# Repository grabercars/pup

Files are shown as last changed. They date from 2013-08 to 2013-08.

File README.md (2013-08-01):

Cerberus Pup
========

Derivative of the Rostock 3D delta printer - 

[cc by sa 3.0]

Cerberus Pup
========

7/31/2013

Cerberus Pup is an experimental 3D Delta Robot printer that uses spectra filament for the vertical carriage drive system instead of traditional toothed belts. Please be aware that there will probably (and most likely) be significant changes and improvements made to this design. - A photo gallery of the Ceberus prototype can be found in the G+ gallery here: http://tinyurl.com/CerberusPup

A BOM is available here - http://tinyurl.com/Pup-BOM-Google-Spreadsheet - there are still some issues with the BOM, please contact Steve Graber to help correct any issues you find.

Print Files:

Qty - Filename

3 - 1x.125 aluminum bar.pdf

3 - 2x.125 aluminum bar.pdf

1 - Extruder_Lever.stl

1 - Extruder_Mount.stl

1 - Jslot_insert.stl

1 - JSlot_plate.stl

1 - Platform_and_Shroud_Assem_Traxxas.stl

1 - Pup_Base_Template.PDF

3 - Pup_Bottom_Bracket.stl

3 - Pup_Upper_Bracket.stl

3 - Pup_Upper_Idler_Adjuster_Bearing_Carrier.stl

3 - Upper_Idler_Axle_airtripper.stl

3 - Pup_Vertical_Carriage.stl

2 - VIKI_LCD_Panel_Side_Mounting_Bracket.stl

1 - Viki_Panel_Surround.stl

2 - Viki_to_Pup_Hangar_Bracket.stl (mirror 2nd copy)

Experimental Files: 

1 - Platform_Geomag_v2_with_shroud.stl

1 - Pup_vert_carriage_Geomag_v2.stl

You will need to print a set of Xnaron magnetic rods available here: http://www.thingiverse.com/thing:87839 - Your printer needs to be very accurate and you will have problems aligning the steel balls perfectly on the platform. This is why this feature is experimental as it was difficult to attach the balls to the ends of bolts with epoxy with any dimensional consistency.

Notes:

All machined parts required to build Cerberus Pup are now all available for purchase at http://3d.grabercars.com. They are manufactured on a CNC lathe to very tight tolerances.

SPECTRA FILAMENT VERTICAL CARRIAGE DRIVE SYSTEM:
Cerberus does not use belts or leadscrews. It uses a very strong braided filament called spectra. This is commonly used as fishing line. Cerberus uses 65lb test line. The drive system requires a threaded 'spool' or 'drive reel' that grabs the spectra very securely. CNC machined delrin filament drive reels are now available for purchase at 3d.grabercars.com - It is not recommended to use 3D printed drive reels because the print accuracy of your printer will suffer.

VERTICAL CARRIAGES:
The Cerberus vertical carriages move up and down the extrusion towers by rolling on 3 cnc machined delrin 'w' rollers per carriage. Each roller consists of a cnc machined delrin cover with two 623 bearing pressed in. The roller rides in the T-Slot of the OpenBeam or Misumi 1515 extrusion. This makes for a very smooth and accurate linear carriage system. Dual 623 V Rollers  can be purchased from 3d.grabercars.com

FILAMENT TENSION SYSTEM:
Due to the high tension required of the spectra filament drive, the upper idler adjuster bearing carrier requires one machined delrin V-Groove idler filament bearing per vertical tower, riding on an 8mm shaft. This upper idler bearing transfers the upward motion of the spectra filament at the top of the printer towers into downward motion. I used a printed 8mm idler bearing shaft borrowed from Airtrippers Bowden extruder (Search www.thingiverse.com) and manufactured the delrin V-Groove idlers with 8mm I.D. hole on a CNC lathe.

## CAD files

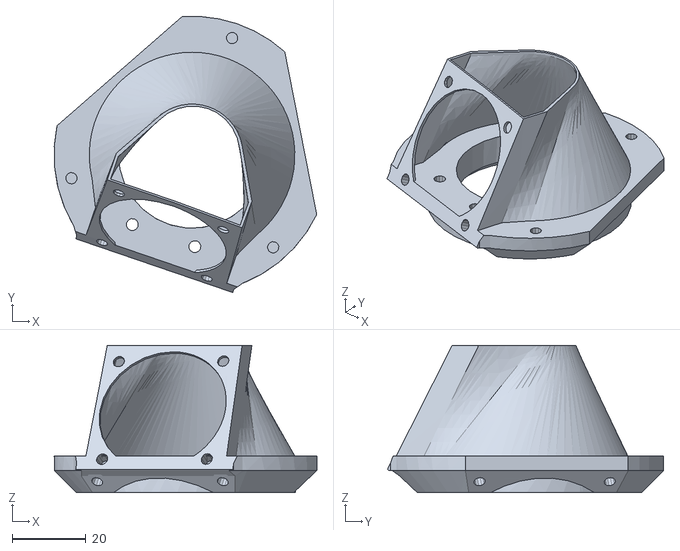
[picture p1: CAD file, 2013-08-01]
experimental/platform_Geomag_v2_with_shroud.STL
71.2 x 74.9 x 40.0

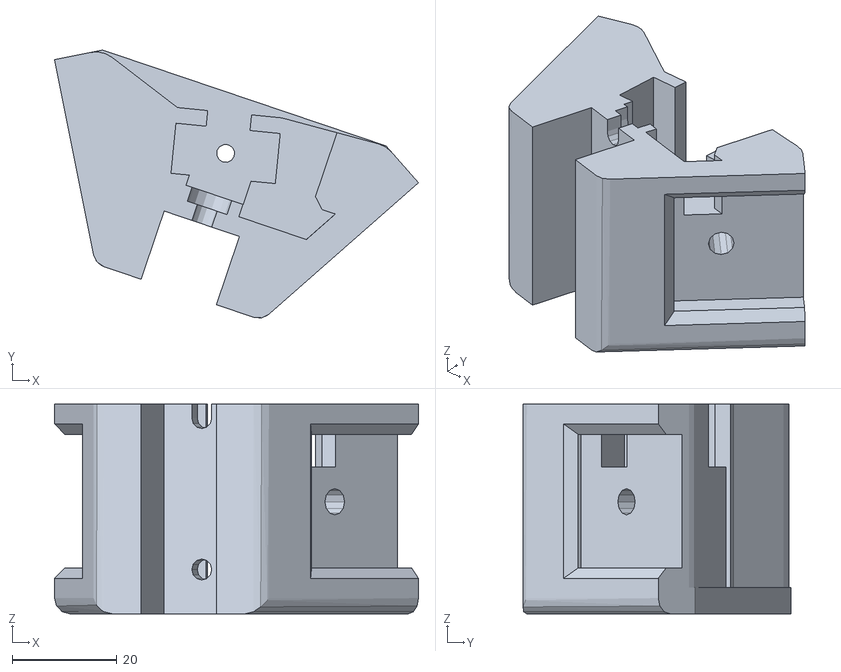
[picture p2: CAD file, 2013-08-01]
Pup_Upper_Bracket.stl
69.4 x 51.1 x 40.0

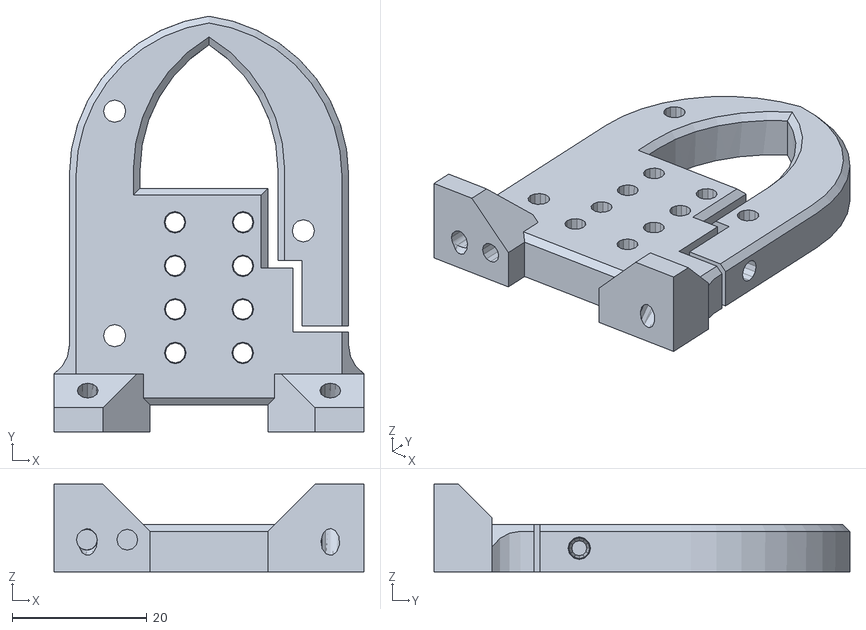
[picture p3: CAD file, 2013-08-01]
experimental/Pup_vert_carriage_Geomag_v2.STL
46.0 x 61.7 x 13.0

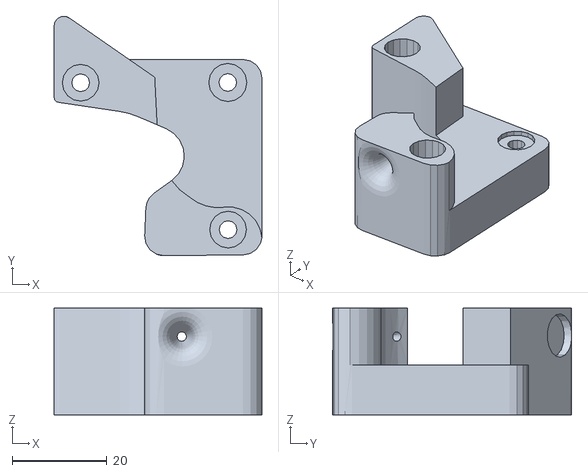
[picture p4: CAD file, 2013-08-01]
Extruder_Mount.stl
43.8 x 50.4 x 22.5

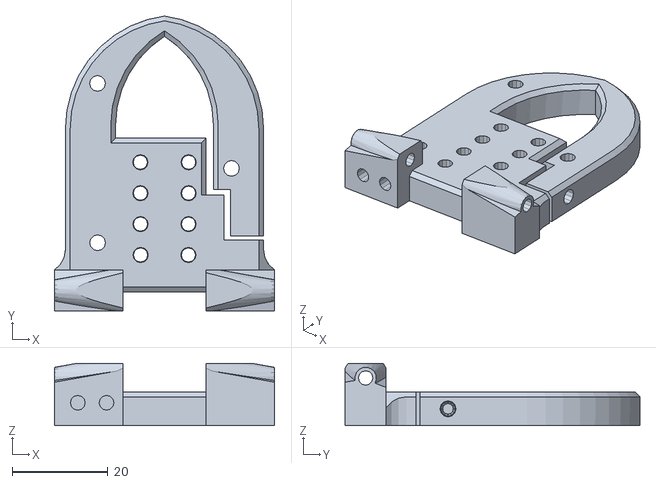
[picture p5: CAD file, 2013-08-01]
Pup_Vertical_Carriage.stl
46.0 x 61.7 x 13.0

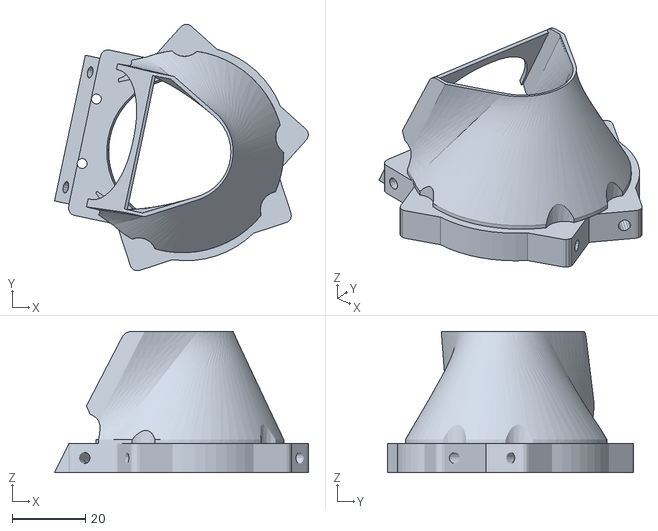
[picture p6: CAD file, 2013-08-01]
Platform_and_Shroud_Assem_Traxxas.stl
69.1 x 67.1 x 38.5

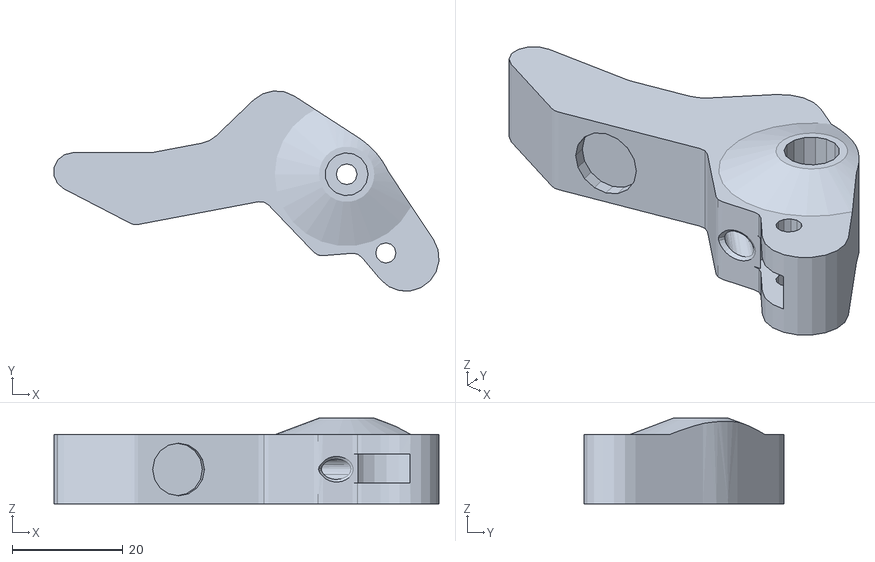
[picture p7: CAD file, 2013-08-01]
Extruder_Lever.stl
69.6 x 36.2 x 15.5

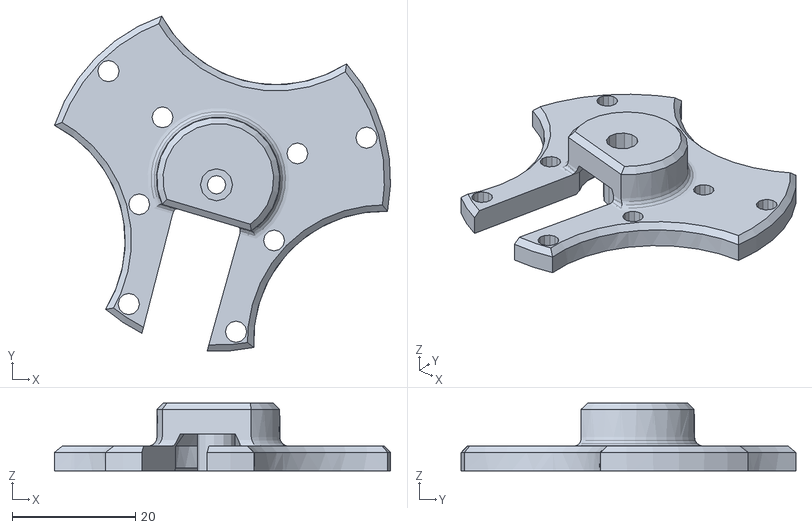
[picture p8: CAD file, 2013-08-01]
JSlot_plate.stl
54.6 x 54.4 x 11.0

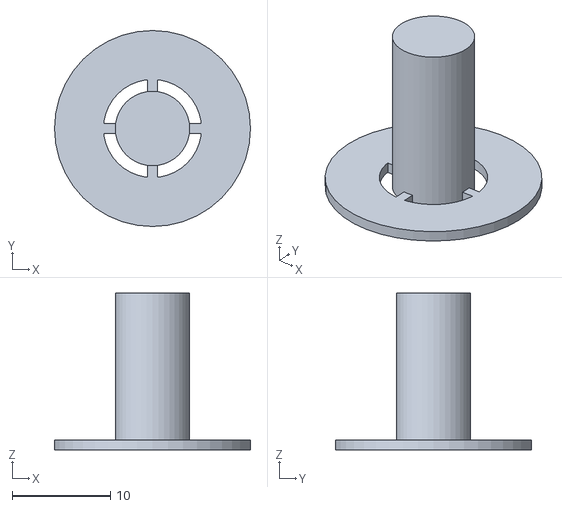
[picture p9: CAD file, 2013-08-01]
Upper_Idler_Axle_airtripper.stl
20.0 x 20.0 x 16.0

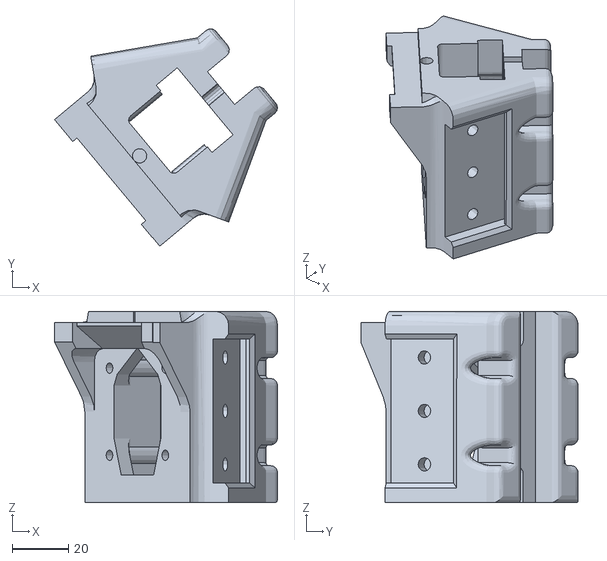
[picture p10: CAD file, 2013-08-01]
Pup_Bottom_Bracket.stl
79.3 x 77.2 x 68.0

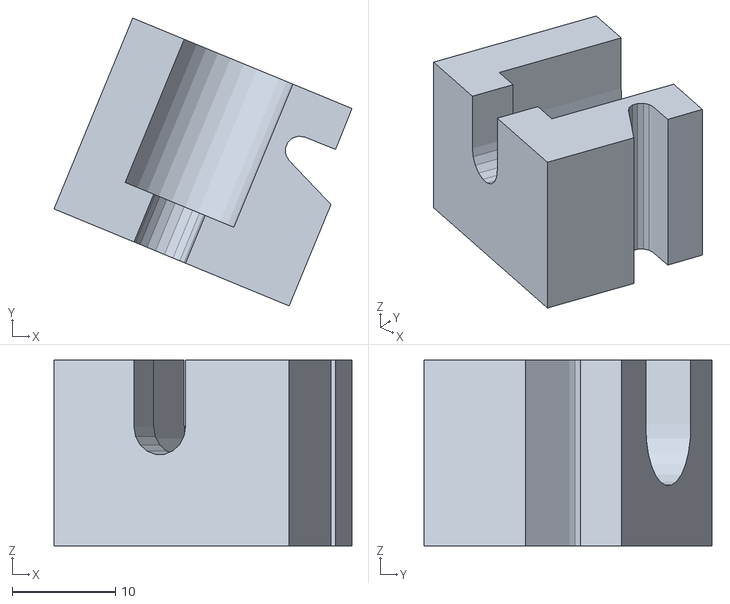
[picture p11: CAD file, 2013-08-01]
Viki_to_Pup_Hangar_Bracket.stl
28.9 x 27.9 x 18.0

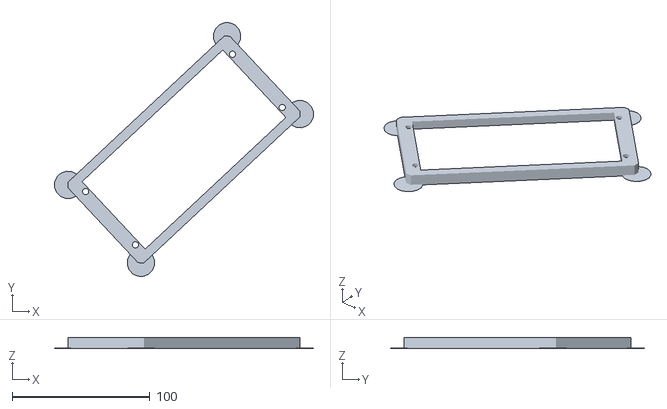
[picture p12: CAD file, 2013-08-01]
Viki_Panel_Surround.stl
187.8 x 184.0 x 8.00

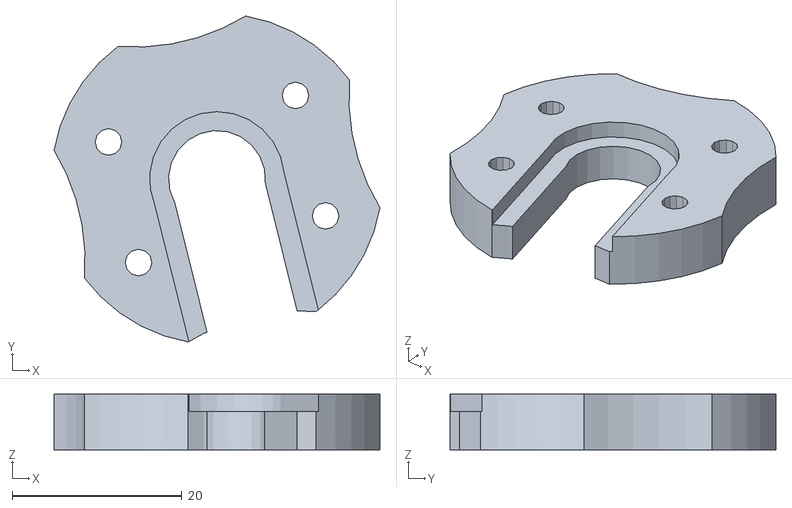
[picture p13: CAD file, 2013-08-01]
Jslot_insert.stl
38.4 x 38.4 x 6.56

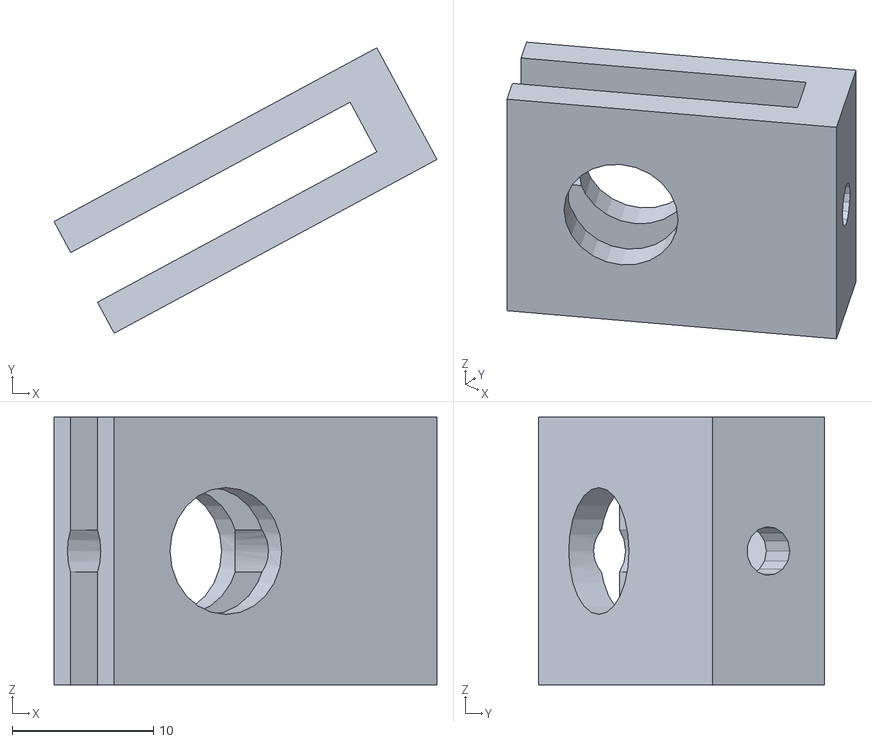
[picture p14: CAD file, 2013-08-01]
Pup_Upper_Idler_Adjuster_Bearing_Carrier.stl
27.2 x 20.3 x 19.0

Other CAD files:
VIKI_LCD_Panel_Side_Mounting_Bracket.stl

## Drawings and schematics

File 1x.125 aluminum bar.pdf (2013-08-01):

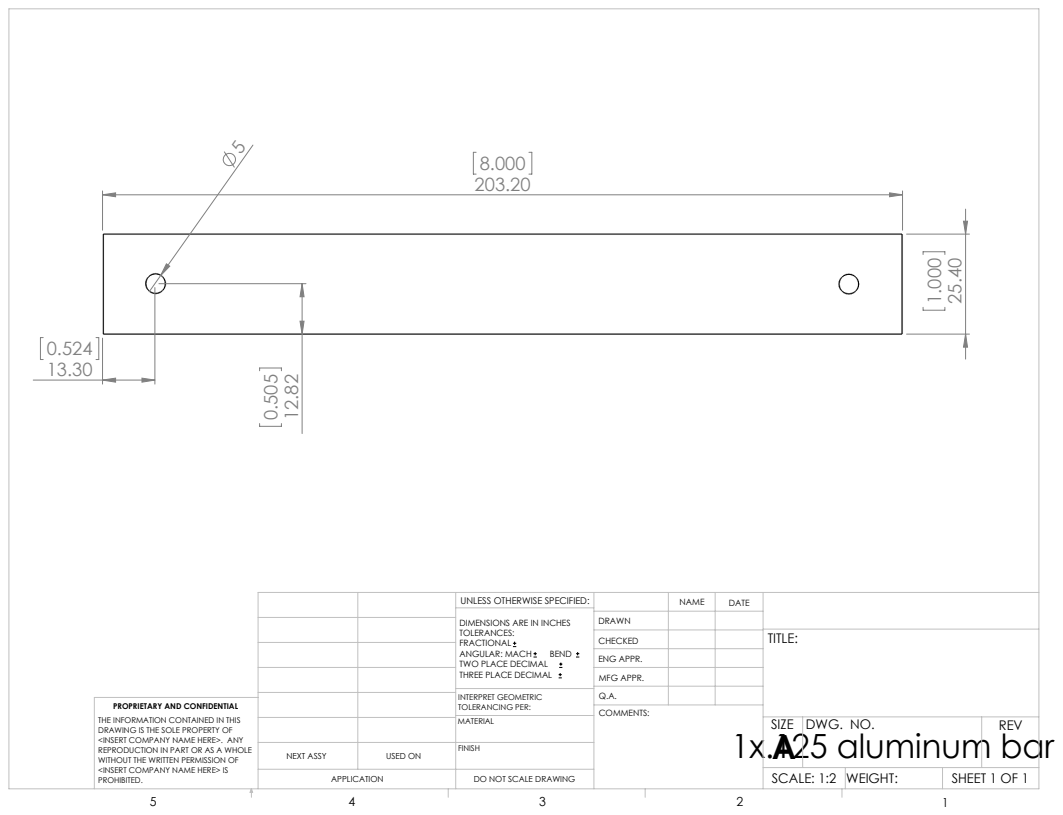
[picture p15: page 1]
1x.125 aluminum bar; SHEET 1 OF 1; SCALE: 1:2 WEIGHT:; DWG. NO.; REV; MFG APPR.; ENG APPR.; INTERPRET GEOMETRIC TOLERANCING PER:; ANGULAR: MACH; BEND; NEXT ASSY; USED ON

UNLESS OTHERWISE SPECIFIED:

DIMENSIONS ARE IN INCHES
TOLERANCES:
FRACTIONAL
TWO PLACE DECIMAL
THREE PLACE DECIMAL

PROPRIETARY AND CONFIDENTIAL
THE INFORMATION CONTAINED IN THIS
DRAWING IS THE SOLE PROPERTY OF
<INSERT COMPANY NAME HERE>. ANY
REPRODUCTION IN PART OR AS A WHOLE
WITHOUT THE WRITTEN PERMISSION OF
<INSERT COMPANY NAME HERE> IS
PROHIBITED.

DO NOT SCALE DRAWING

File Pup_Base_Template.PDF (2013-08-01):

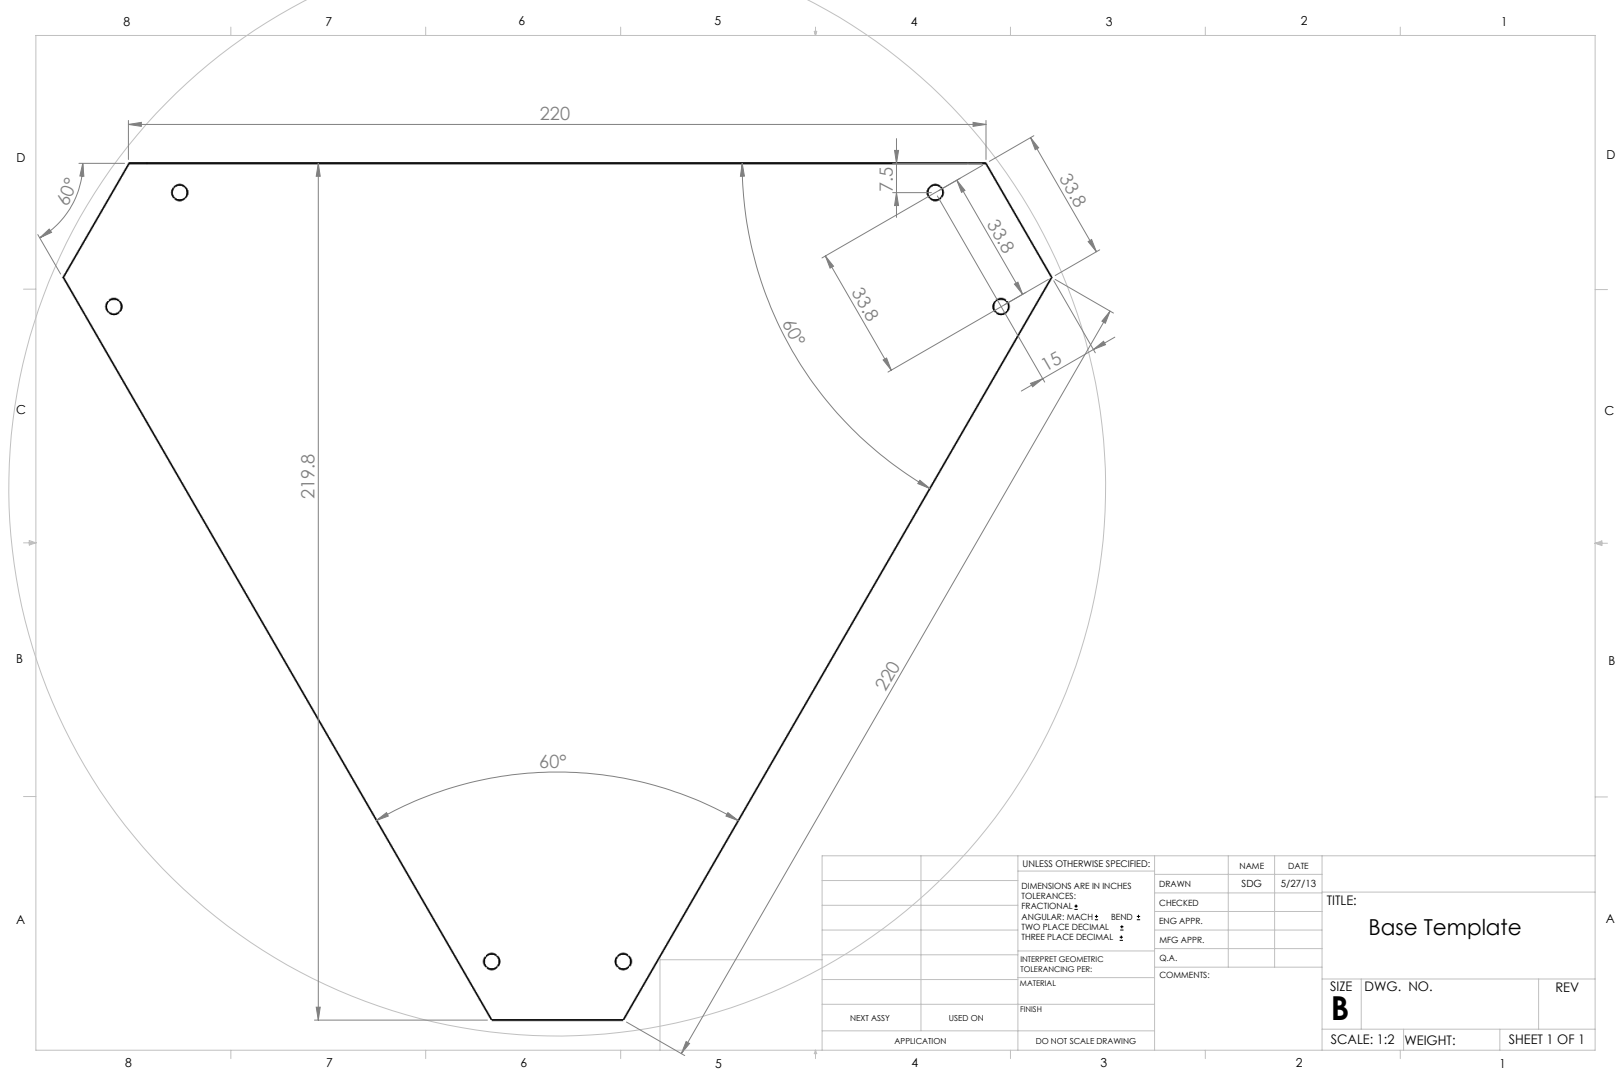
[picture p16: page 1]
NEXT ASSY; USED ON; ANGULAR: MACH; BEND; INTERPRET GEOMETRIC TOLERANCING PER:; ENG APPR.; MFG APPR.; DWG. NO.; REV; SCALE: 1:2 WEIGHT:; SHEET 1 OF 1; Base Template

UNLESS OTHERWISE SPECIFIED:

DIMENSIONS ARE IN INCHES
TOLERANCES:
FRACTIONAL
TWO PLACE DECIMAL
THREE PLACE DECIMAL

DO NOT SCALE DRAWING

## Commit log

2013-08-01 Initial Commit of Cerberus Pup 170mm round bed spectra filament drive deltabot 3D printer
    [Extruder_Lever.stl, Extruder_Mount.stl, JSlot_plate.stl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]
2013-08-01 Added a link to the Google Spreadsheet Pup BOM
